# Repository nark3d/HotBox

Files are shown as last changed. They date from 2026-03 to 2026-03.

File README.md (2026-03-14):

# HotBox

HotBox - a tiny enclosure heater

## Contents

- [Disclaimer](#-disclaimer-)
- [BOM](#bom)
- [Note](#note)
- [Installation Instructions](#installation-instructions)
- [Klipper Config](#klipper-config)
- [Gotchas](#gotchas)
- [Inspiration and Credit](#inspiration-and-credit)

<p align="center">
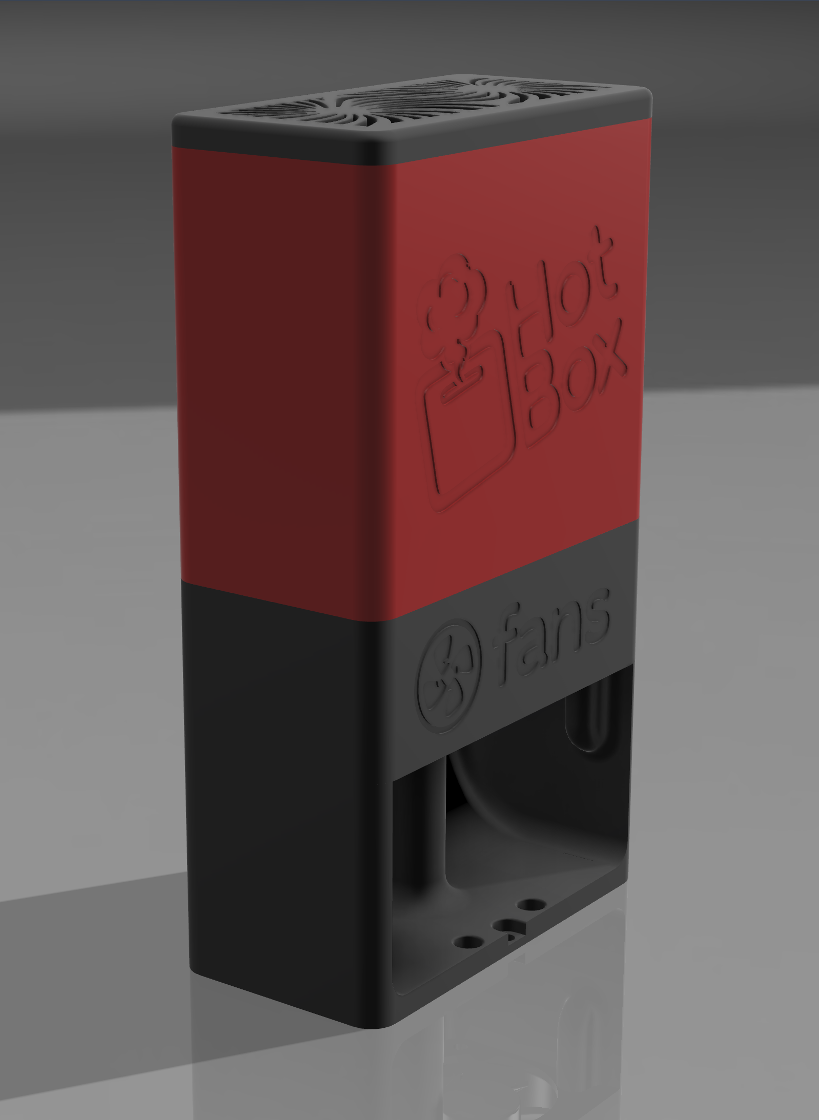
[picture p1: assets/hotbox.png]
HotBox

</p>

<p align="center"><em>100mm wide, 52mm deep and 177mm high</em></p>

<p align="center">
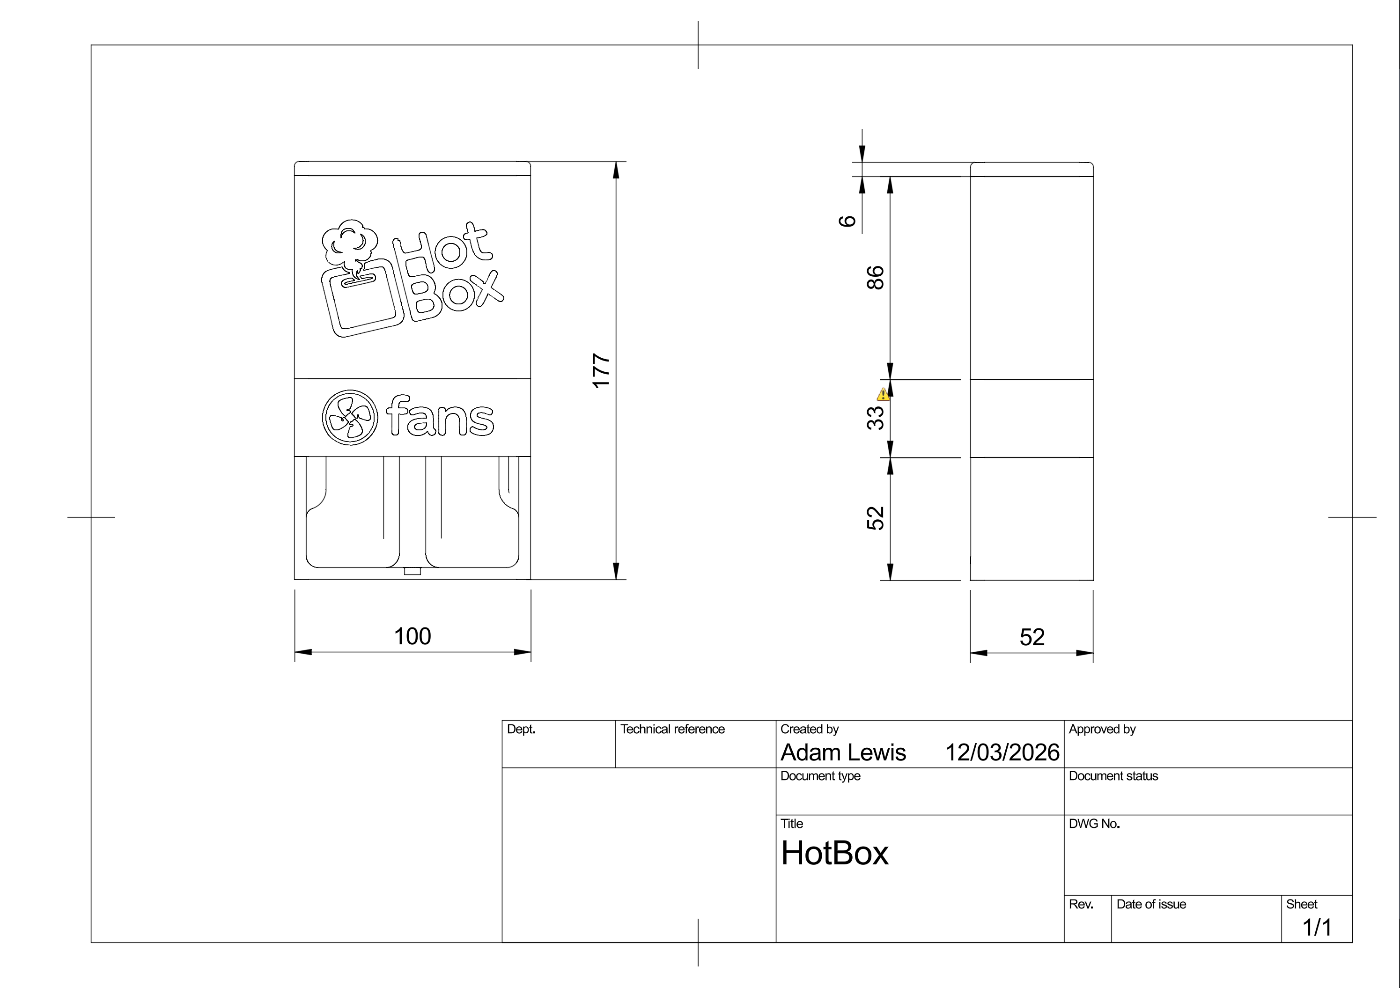
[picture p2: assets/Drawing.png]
HotBox Technical Drawing

</p>

# 🔥 Disclaimer 🔥

> [!WARNING]
> HotBox uses a resistive heating element inside an enclosed space. Built and configured incorrectly, it is a genuine fire risk.
>
> This project is shared as-is for experienced makers who understand the risks. The author accepts no responsibility for damage, injury, or loss of any kind. You build and run this entirely at your own risk.
>
> If you're not comfortable working with high-current DC systems and thermal management, please don't attempt this build.

# BOM

<p align="center">
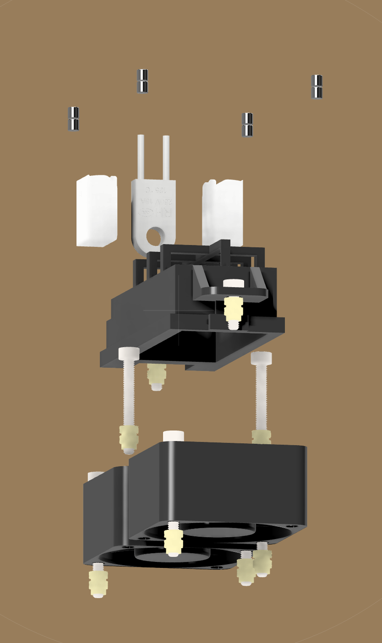
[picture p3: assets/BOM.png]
BOM

</p>

<p align="center">
<video src="https://github.com/user-attachments/assets/a794df79-9960-4280-891d-2e4521b5a101" width="50%" controls></video>
</p>

<table>
  <thead>
    <tr>
      <th>#</th>
      <th>Image</th>
      <th>Part</th>
      <th>Description</th>
      <th>Qty</th>
      <th>Notes</th>
      <th>Link</th>
    </tr>
  </thead>
  <tbody>
    <tr>
      <td>1</td>
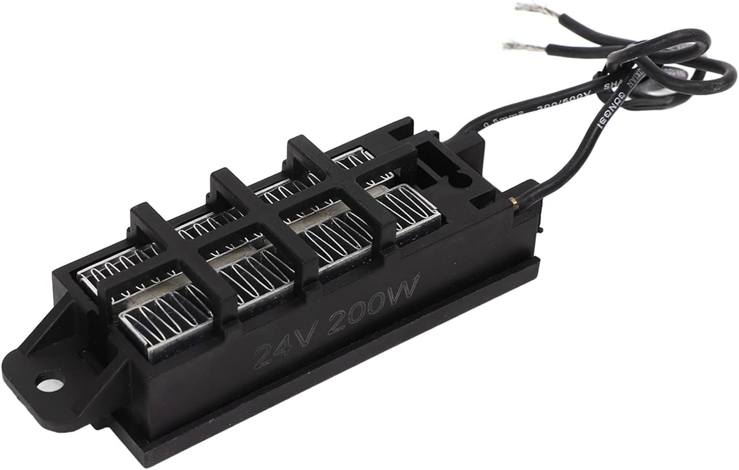
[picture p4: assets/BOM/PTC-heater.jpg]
PTC Heater
      <td></td>
      <td>PTC Heater Element</td>
      <td>24V 200W ceramic PTC heater</td>
      <td align="center">1</td>
      <td>Self-limiting; derate above 87°C</td>
      <td><a href="https://www.amazon.co.uk/dp/B0DK5W3RKS">amazon.co.uk</a></td>
    </tr>
    <tr>
      <td>2</td>
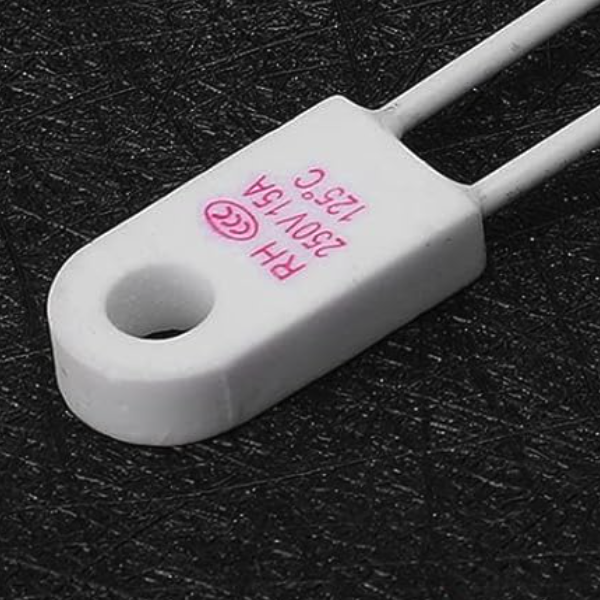
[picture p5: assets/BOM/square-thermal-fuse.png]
Thermal Fuse
      <td></td>
      <td>Square Thermal Fuse</td>
      <td>125°C Ceramic Thermal 250V 15A</td>
      <td align="center">1</td>
      <td>CQC rated; soldered inline</td>
      <td><a href="https://www.amazon.co.uk/dp/B0BNQ7SJYP">amazon.co.uk</a></td>
    </tr>
    <tr>
      <td>3</td>
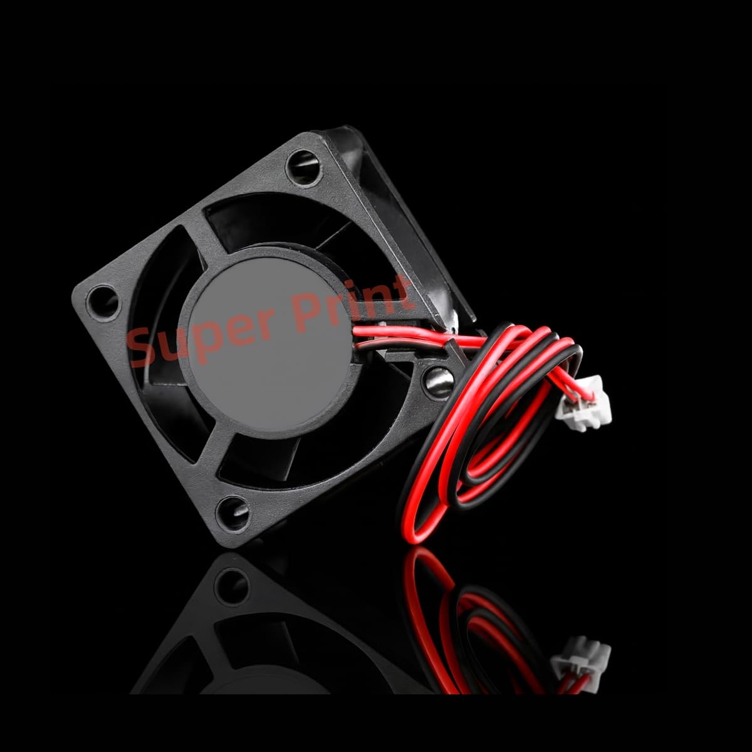
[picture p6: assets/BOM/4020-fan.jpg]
4020 Fan
      <td></td>
      <td>Axial Fan</td>
      <td>24V 4020 axial fan</td>
      <td align="center">2</td>
      <td>Must run at 100% when element is powered</td>
      <td><a href="https://www.amazon.co.uk/dp/B0FRFMXKSX">amazon.co.uk</a></td>
    </tr>
    <tr>
      <td>4</td>
      <td>
        <a href="assets/BOM/NTC-100K-thermistor-OD3mm.jpg">
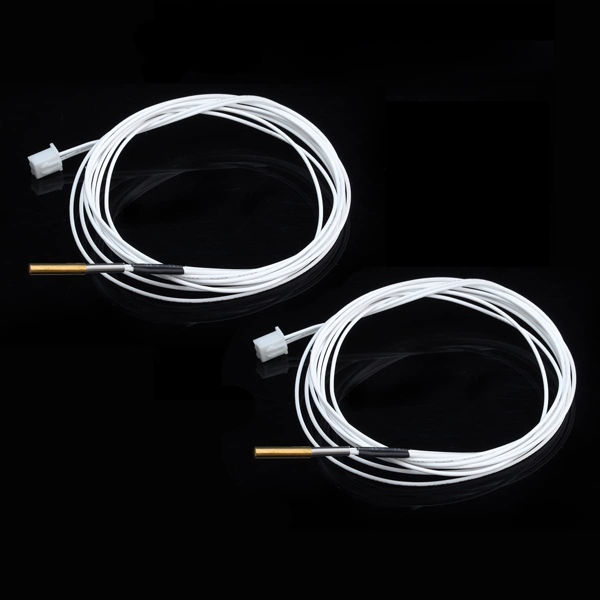
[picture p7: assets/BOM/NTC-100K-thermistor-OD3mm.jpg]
NTC 100K thermistor
            
        </a>
      </td>
      <td>Thermistor</td>
      <td>NTC 100K</td>
      <td align="center">1</td>
      <td>Seats in dedicated hole in PTC body; use thermal glue</td>
      <td><a href="https://www.amazon.co.uk/dp/B0BDFHZZQX?">amazon.co.uk</a></td>
    </tr>
    <tr>
      <td>5</td>
      <td>
        <a href="assets/BOM/thermal-glue.jpg">
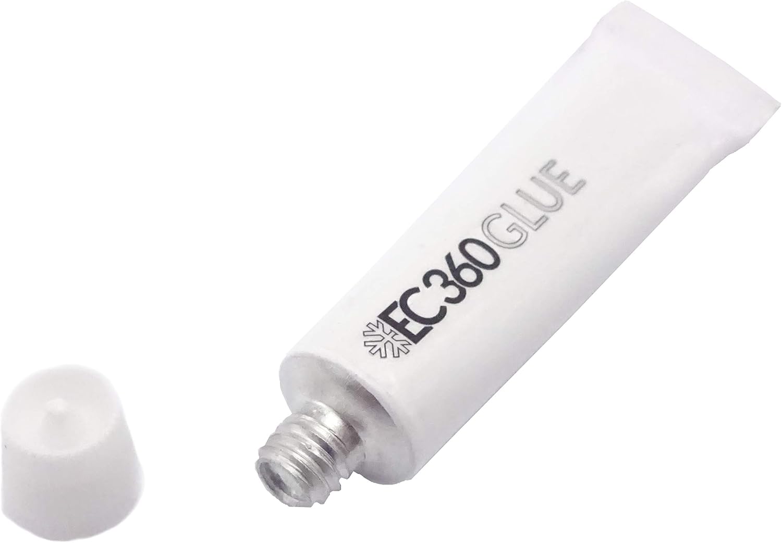
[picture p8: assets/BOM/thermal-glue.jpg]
Thermal glue
          
        </a>
      </td>
      <td>Thermal Glue</td>
      <td>EC360 2W/mK thermal adhesive</td>
      <td align="center">1</td>
      <td>Bonds thermistor to PTC element body</td>
      <td><a href="https://www.amazon.co.uk/dp/B00XQ9AZ8Y">amazon.co.uk</a></td>
    </tr>
    <tr>
      <td>6</td>
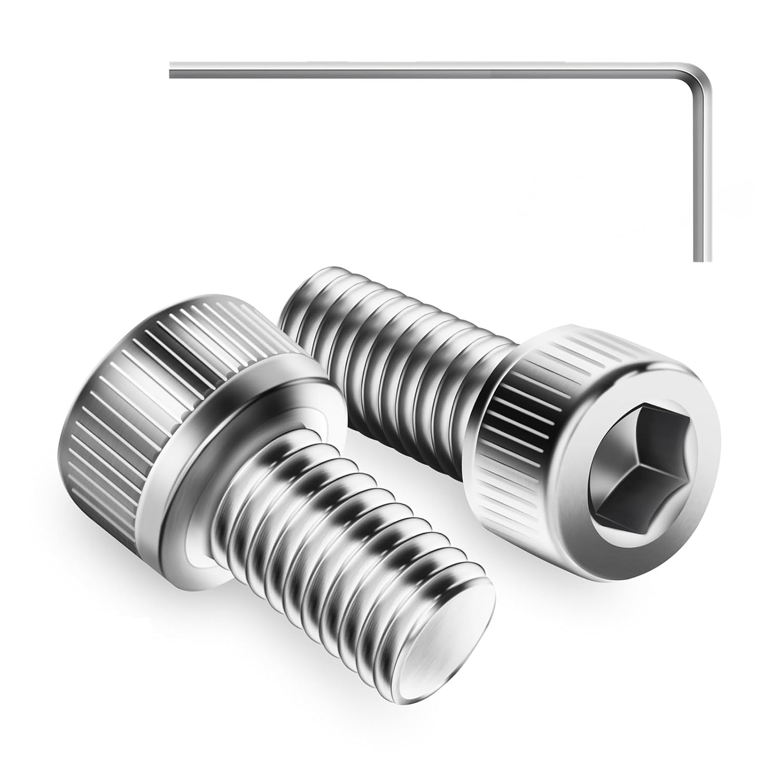
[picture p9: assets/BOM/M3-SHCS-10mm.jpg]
M3 SHCS
      <td></td>
      <td>M3×10mm SHCS</td>
      <td>Socket head cap screw</td>
      <td align="center">2</td>
      <td>Secures PTC heater element</td>
      <td></td>
    </tr>
    <tr>
      <td>7</td>
      <td><a href="assets/BOM/M3-SHCS-10mm.jpg">M3 SHCS</a></td>
      <td>M3×25mm SHCS</td>
      <td>Socket head cap screw</td>
      <td align="center">2</td>
      <td>Heater case to fan case</td>
      <td></td>
    </tr>
    <tr>
      <td>8</td>
      <td><a href="assets/BOM/M3-SHCS-10mm.jpg">M3 SHCS</a></td>
      <td>M3×30mm SHCS</td>
      <td>Socket head cap screw</td>
      <td align="center">4</td>
      <td>Fans through to fan duct</td>
      <td></td>
    </tr>
    <tr>
      <td>9</td>
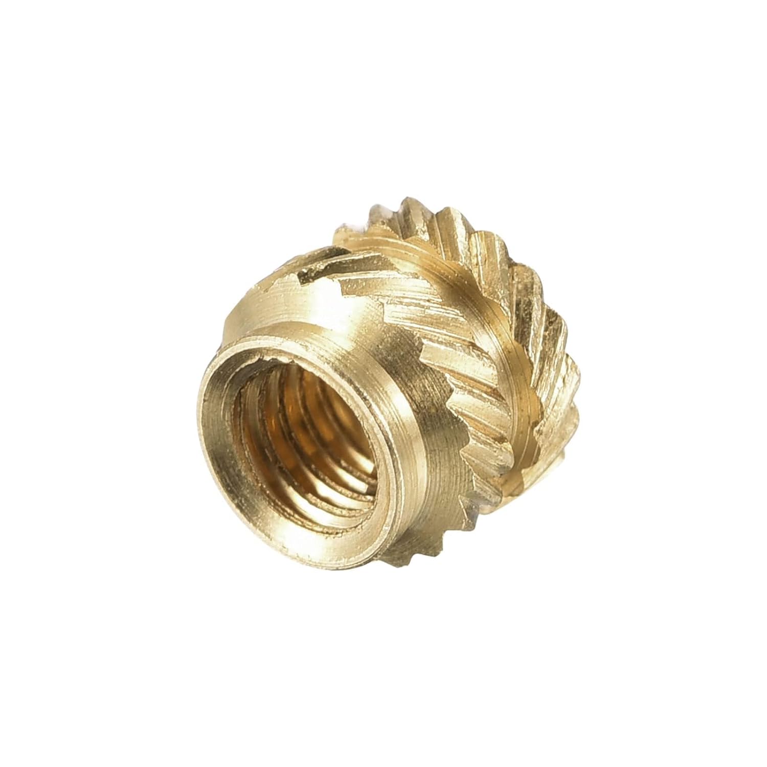
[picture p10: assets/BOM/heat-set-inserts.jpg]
Heat-Set Insert
      <td></td>
      <td>Heat-Set Insert</td>
      <td>M3×4mm brass heat-set insert</td>
      <td align="center">8</td>
      <td></td>
      <td><a href="https://www.amazon.co.uk/dp/B0DC6RXRB9">amazon.co.uk</a></td>
    </tr>
    <tr>
      <td>10</td>
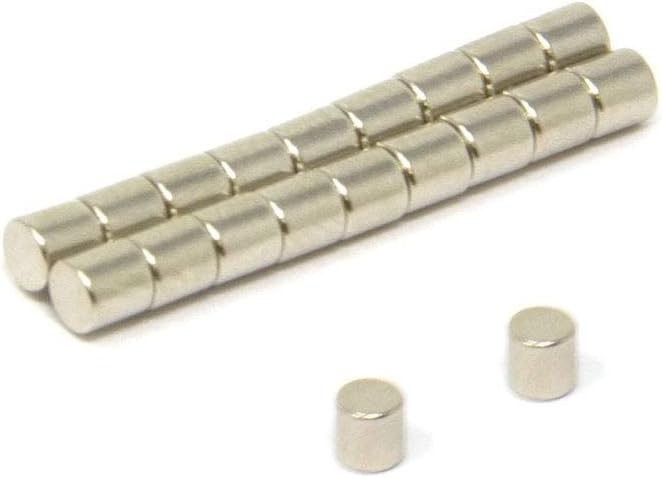
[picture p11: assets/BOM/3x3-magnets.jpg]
3x3mm Magnets
      <td></td>
      <td>Magnets</td>
      <td>3×3mm N42 neodymium magnets</td>
      <td align="center">8</td>
      <td>For lid retention</td>
      <td><a href="https://www.amazon.co.uk/dp/B00389GIK6">amazon.co.uk</a></td>
    </tr>
    <tr>
      <td>11</td>
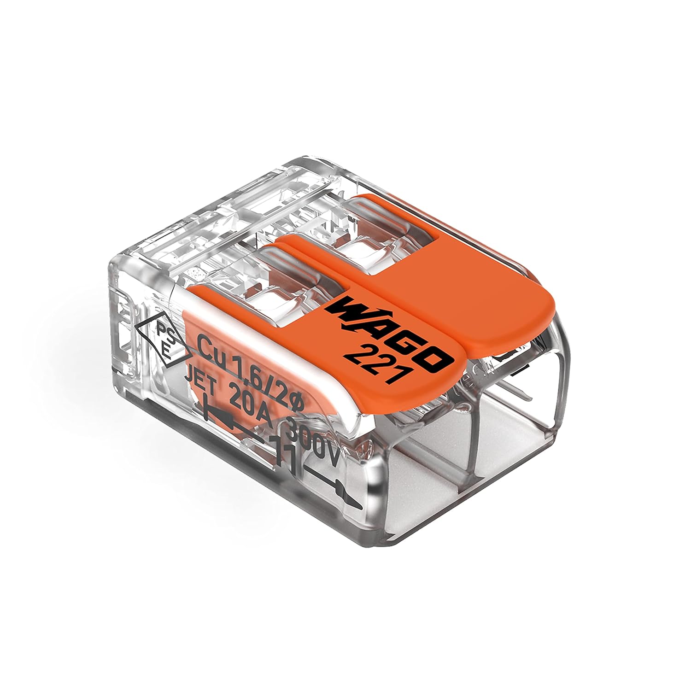
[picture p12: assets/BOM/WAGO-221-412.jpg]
WAGO 221-412
      <td></td>
      <td>WAGO 221-412</td>
      <td>2-conductor lever-nut splicing connector</td>
      <td align="center">3</td>
      <td>Tool-free wire connections for heater, fans and thermistor</td>
      <td><a href="https://www.amazon.co.uk/dp/B07W4RQ6R6">amazon.co.uk</a></td>
    </tr>
    <tr>
      <td>12</td>
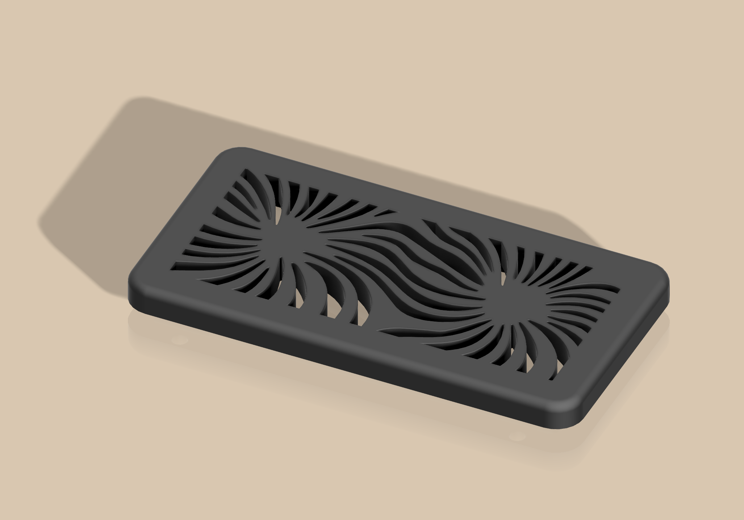
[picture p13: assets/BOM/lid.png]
Lid
      <td></td>
      <td>Lid</td>
      <td>Printed part</td>
      <td align="center">1</td>
      <td>Print in ABS/ASA</td>
      <td><a href="STLs/hotbox-lid-v1.0.stl">STL</a></td>
    </tr>
    <tr>
      <td>13</td>
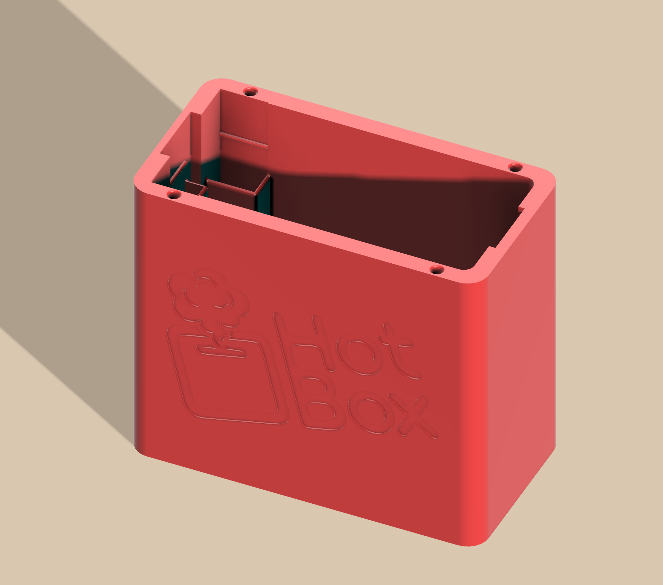
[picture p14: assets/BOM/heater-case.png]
Heater Case
      <td></td>
      <td>Heater Case</td>
      <td>Printed part</td>
      <td align="center">1</td>
      <td>Print in ABS/ASA</td>
      <td><a href="STLs/hotbox-heater-case-v9.3.stl">STL</a></td>
    </tr>
    <tr>
      <td>14</td>
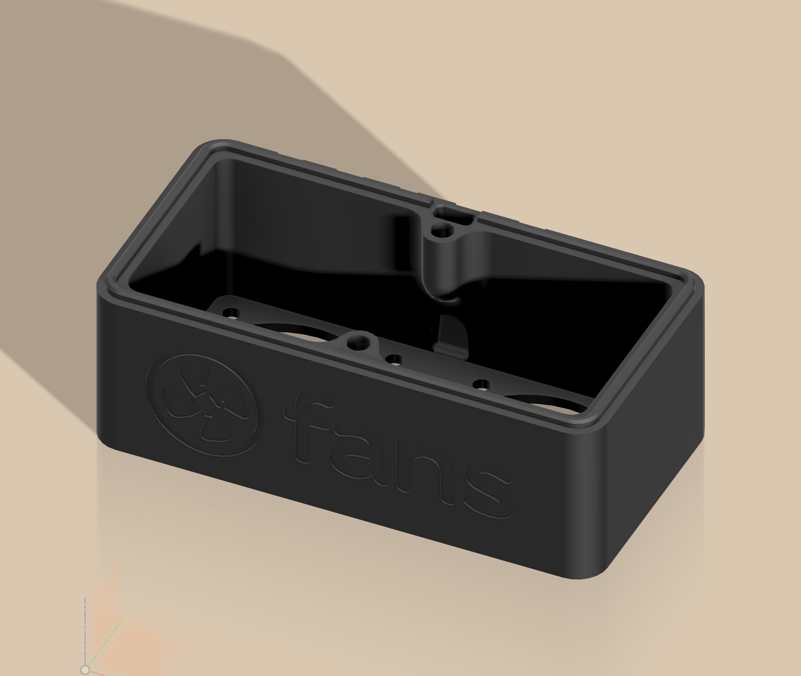
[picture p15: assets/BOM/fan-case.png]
Fan Case
      <td></td>
      <td>Fan Case</td>
      <td>Printed part</td>
      <td align="center">1</td>
      <td>Print in ABS/ASA</td>
      <td><a href="STLs/hotbox-fan-case-v4.2.stl">STL</a></td>
    </tr>
    <tr>
      <td>15</td>
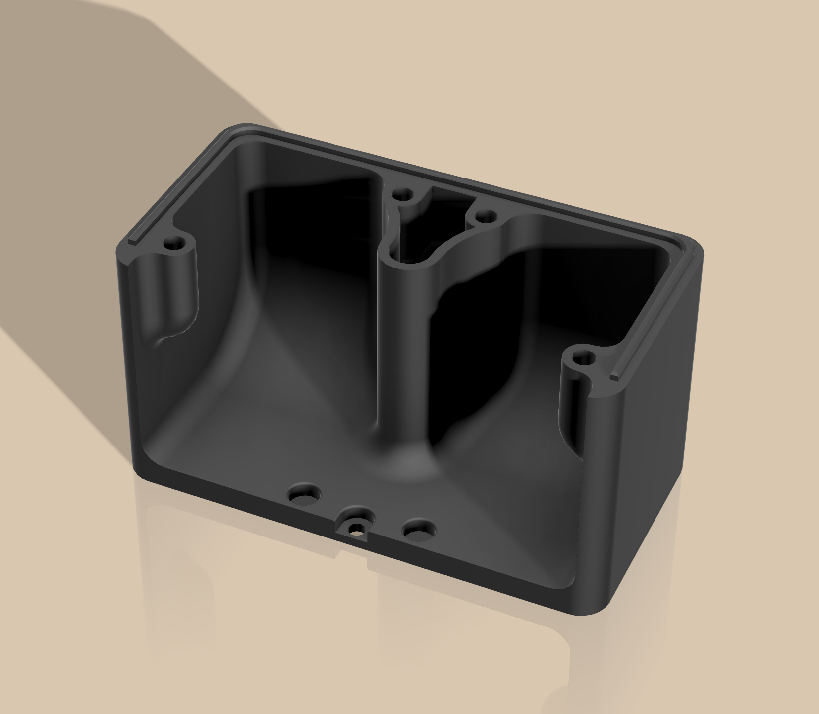
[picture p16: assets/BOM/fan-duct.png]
Fan Duct
      <td></td>
      <td>Fan Duct</td>
      <td>Printed part</td>
      <td align="center">1</td>
      <td>Print in ABS/ASA</td>
      <td><a href="STLs/hotbox-fan-duct-v2.1.stl">STL</a></td>
    </tr>
    <tr>
      <td>16</td>
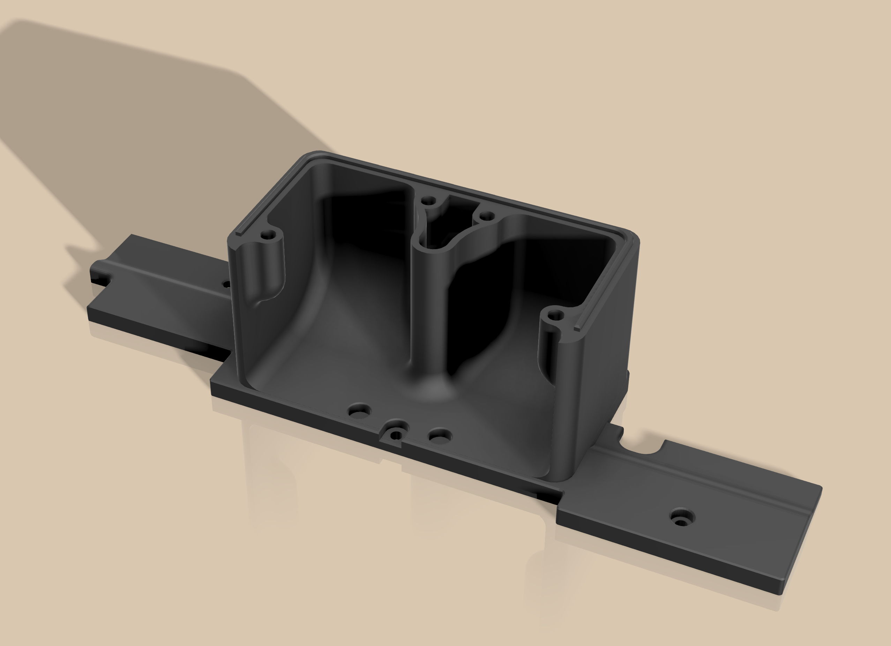
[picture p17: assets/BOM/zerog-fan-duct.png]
Fan Duct ZeroG Nebula
      <td></td>
      <td>Fan Duct ZeroG Nebula</td>
      <td>Printed part</td>
      <td align="center">1</td>
      <td>Print in ABS/ASA; alternative duct for ZeroG Nebula enclosure</td>
      <td><a href="STLs/hotbox-fan-duct-zerog-nebula-v2.1.stl">STL</a></td>
    </tr>
  </tbody>
</table>

# Note

<p align="center">
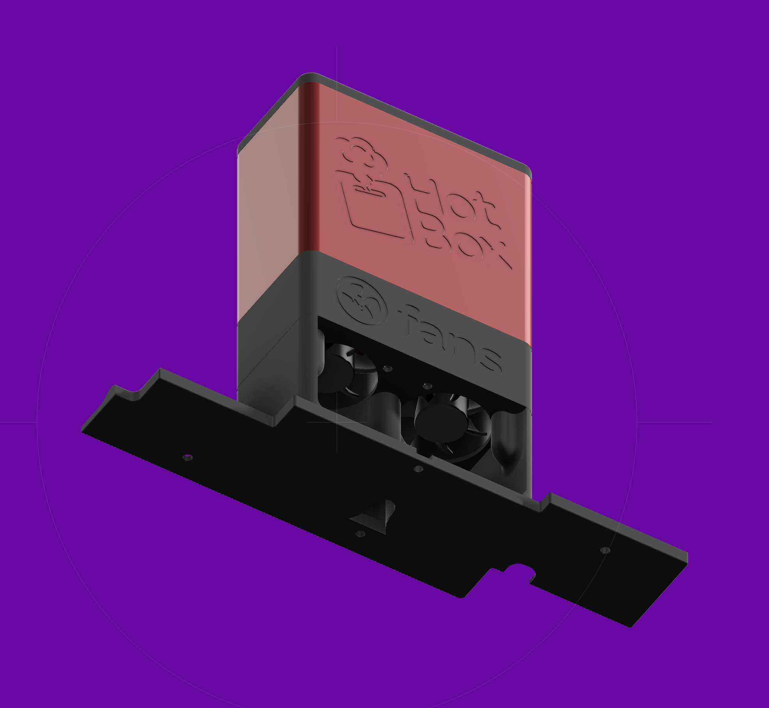
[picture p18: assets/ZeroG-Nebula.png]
ZeroG-Nebula

</p>

I made this for me on my ZeroG Nebula printer. I've provided a fan duct without the filler plate which will bolt onto a 2020 extrusion, but I'm not going to try and build mounting solutions for other printers without being able to test or measure.

If you want to use this heater on your printer, either:

- Modify the fan duct, test it, let me know and it can be added to the repo
- spec out what you need and I'll build it, (untested) and publish it

# Installation instructions

(Pictures to follow soon)

## Main body

- Fit all heat-set inserts into the correct holes with a soldering iron
- Trim the ends of the thermal fuse so that the wires fit neatly into the wagos without touching the lid
- Cut one side of the PTC thermal heater wire to length so that it fits in the wag opposite the cable hole without pushing the lid
- Fill the round hole in the PTC heater with thermal glue and insert the thermistor and wait to DRY (this will not cure until up to temperature later)
- Slot the WAGO's and thermal fuse into the correct holes
- Feed the wires through the cable hole. This will be SUPER TIGHT! The hole is as large as it can be whilst maintaining the small size of the heater
- Before pulling all the wires completely through, put the wired end of the PTC heater under the thermal fuse holder and then slot in the front. Wiggle it a bit and get it into position
- Screw down the PTC heater
- Pull the wires through so that they are neat and not obstructing the heater
- Push the wires through the fan case and down through the middle hole, but do not tighten
- Put the fans in the right position in the fan case - airflow going up into the PTC element
- Feed the fan wires through the middle hole
- Feed everything through the middle hole of the fan duct (you may need to join the PTC wire to a new piece of wire and shield it)
- Screw the fan case to the fan duct
- Keeping the wires tight with one hand push it all together
- Screw the heater case to the fan case
- Use a drop of superglue in the magnet holes and tap/push/force them in with something hard

## Electronics

<p align="center">
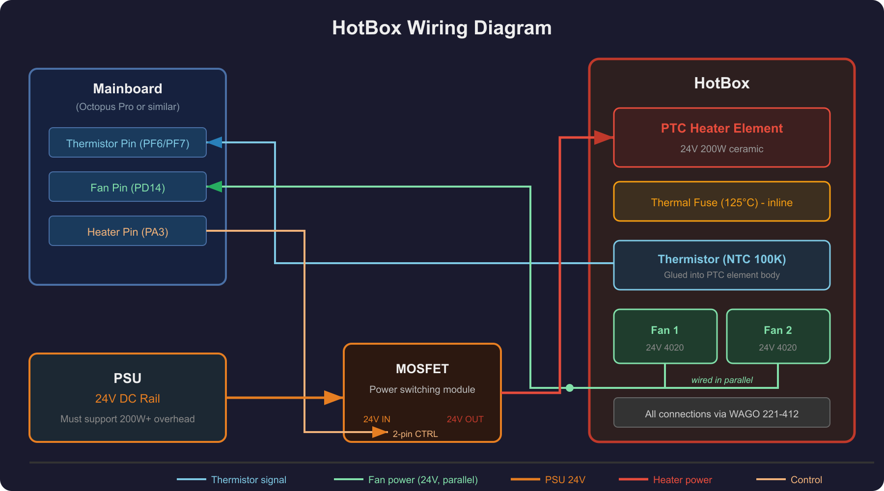
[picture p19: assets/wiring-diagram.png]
HotBox Wiring Diagram

</p>

This is very much dependent on your setup, but I did the following:

- Used WAGO's on the printer body to connect everything together to keep it neat
- Used a Mosfet running off the PSU and a fan PIN to modulate it
- Connected the thermistor and fans to the main board
- Configured everything in Klipper (see below)

# Klipper config

## printer.cfg

```ini
# ============================================================
# HOTBOX Config
# ============================================================

[heater_generic chamber]
heater_pin: PA3 # <---------------  change this
sensor_type: Generic 3950
sensor_pin: PF6 # <---------------  change this
min_temp: 0
max_temp: 70
control: pid
pwm_cycle_time: 0.01
pid_Kp: 100
pid_Ki: 0.3
pid_Kd: 30

[verify_heater chamber]
max_error: 600
check_gain_time: 300
hysteresis: 5
heating_gain: 0.5

# Fans will run at 100% any time the hotbox element exceeds 35, regardless
# of what Klipper is doing (PID calibration, printing, idle, anything).
[temperature_fan hotbox]
pin: PD14 # <---------------  change this
sensor_type: Generic 3950
sensor_pin: PF7 # <---------------  change this
min_temp: 0
max_temp: 120
target_temp: 35.0
min_speed: 0.0
max_speed: 1.0
control: watermark
max_delta: 1
kick_start_time: 0.5

# ============================================================
# HOTBOX CONTROL LOOP
# Runs every 5 seconds from printer startup
# Stores chamber target into HOTBOX_STATE so backoff can restart
# Fan speed is now managed automatically by [temperature_fan hotbox]
# This loop only handles: state tracking + overtemp backoff
# ============================================================
[delayed_gcode HOTBOX_CONTROL]
initial_duration: 5
gcode:
    {% set hotbox_temp = printer['temperature_fan hotbox'].temperature %}
    {% set chamber_target = printer['heater_generic chamber'].target %}
    {% set heater_on = chamber_target > 0 %}
    {% if heater_on %}
        SET_GCODE_VARIABLE MACRO=HOTBOX_STATE VARIABLE=target VALUE={chamber_target}
    {% endif %}
    {% if hotbox_temp > 87 and heater_on %}
        SET_HEATER_TEMPERATURE HEATER=chamber TARGET=0
        UPDATE_DELAYED_GCODE ID=HOTBOX_BACKOFF DURATION=60
        RESPOND MSG="HotBox: Element at {hotbox_temp}C - 60s backoff, will restart automatically"
    {% endif %}
    UPDATE_DELAYED_GCODE ID=HOTBOX_CONTROL DURATION=5

# ============================================================
# HOTBOX BACKOFF TIMER
# Triggered by HOTBOX_CONTROL after element overtemp
# Calls HOTBOX_RESTART after 60 seconds
# ============================================================
[delayed_gcode HOTBOX_BACKOFF]
initial_duration: 0
gcode:
    HOTBOX_RESTART

[include hotbox_macros.cfg] # <---------------  put this with your other includes or at the end of the file

```

## hotbox_macros.cfg

```ini
# ============================================================
# hotbox_macros.cfg
# HotBox enclosure heater user macros
# Include this file from printer.cfg with [include hotbox_macros.cfg]
# ============================================================

# ============================================================
# HOTBOX_STATE
# Stores the intended chamber target so backoff can restart
# This is set both by HOTBOX_ON and by the HOTBOX_CONTROL loop
# so it works whether you use the macro or set temp directly in Mainsail
# ============================================================
[gcode_macro HOTBOX_STATE]
variable_target: 0
gcode:

# ============================================================
# HOTBOX_ON
# Usage: HOTBOX_ON TARGET=60
# Heats enclosure to target temperature (default 60C, max 70C)
# Fans start automatically via [temperature_fan hotbox] - no manual control needed
# ============================================================
[gcode_macro HOTBOX_ON]
description: Heat enclosure to target temperature. Usage: HOTBOX_ON TARGET=60
gcode:
    {% set TARGET = params.TARGET|default(60)|float %}
    {% if TARGET > 70 %}
        RESPOND MSG="HotBox: Target {TARGET}C exceeds safe maximum of 70C - aborting"
    {% elif TARGET < 30 %}
        RESPOND MSG="HotBox: Target {TARGET}C is too low - minimum is 30C"
    {% else %}
        SET_GCODE_VARIABLE MACRO=HOTBOX_STATE VARIABLE=target VALUE={TARGET}
        SET_HEATER_TEMPERATURE HEATER=chamber TARGET={TARGET}
        UPDATE_DELAYED_GCODE ID=HOTBOX_CONTROL DURATION=5
        RESPOND MSG="HotBox: Heating enclosure to {TARGET}C - fans will run automatically"
    {% endif %}

# ============================================================
# HOTBOX_OFF
# Turns heater off and clears stored target
# Fans continue automatically until hotbox element cools below 40C
# ============================================================
[gcode_macro HOTBOX_OFF]
description: Turn off HotBox heater. Fans run automatically until hotbox cools below 40C
gcode:
    SET_GCODE_VARIABLE MACRO=HOTBOX_STATE VARIABLE=target VALUE=0
    SET_HEATER_TEMPERATURE HEATER=chamber TARGET=0
    RESPOND MSG="HotBox: Heater off - fans will run automatically until hotbox cools below 40C"

# ============================================================
# HOTBOX_STATUS
# Prints current hotbox status to console
# ============================================================
[gcode_macro HOTBOX_STATUS]
description: Report current HotBox temperatures and fan status
gcode:
    {% set hotbox_temp = printer['temperature_fan hotbox'].temperature %}
    {% set chamber_temp = printer['heater_generic chamber'].temperature %}
    {% set chamber_target = printer['heater_generic chamber'].target %}
    {% set fan_speed = printer['temperature_fan hotbox'].speed %}
    {% set intended_target = printer['gcode_macro HOTBOX_STATE'].target %}
    RESPOND MSG="HotBox Status:"
    RESPOND MSG="  Chamber temp: {chamber_temp}C / Target: {chamber_target}C"
    RESPOND MSG="  Hotbox element: {hotbox_temp}C"
    RESPOND MSG="  Fan speed: {(fan_speed * 100)|round}%"
    RESPOND MSG="  Stored target: {intended_target}C"

# ============================================================
# HOTBOX_RESTART
# Called automatically after 60s backoff - do not call manually
# Restarts heater using stored target if element has cooled below 75C
# ============================================================
[gcode_macro HOTBOX_RESTART]
description: Internal - restarts heater after backoff cooldown
gcode:
    {% set intended_target = printer['gcode_macro HOTBOX_STATE'].target %}
    {% set hotbox_temp = printer['temperature_fan hotbox'].temperature %}
    {% if intended_target > 0 %}
        {% if hotbox_temp < 70 %}
            SET_HEATER_TEMPERATURE HEATER=chamber TARGET={intended_target}
            RESPOND MSG="HotBox: Element cooled to {hotbox_temp}C - restarting heater to {intended_target}C"
        {% else %}
            RESPOND MSG="HotBox: Element still at {hotbox_temp}C - waiting another 60s"
            UPDATE_DELAYED_GCODE ID=HOTBOX_BACKOFF DURATION=60
        {% endif %}
    {% else %}
        RESPOND MSG="HotBox: No stored target - not restarting"
    {% endif %}
```

# Gotchas

- PID calibration may not work close to the enclosure's thermal limit. If the enclosure cannot reliably reach and re-reach the target temperature through multiple oscillation cycles, the calibration will fail. Try a lower target temperature (e.g. TARGET=50 instead of TARGET=60).

- PTC heater elements are self-limiting — they reduce power output as they approach their rated temperature. This makes PID calibration difficult as the element may throttle itself during the calibration oscillation cycles.

- Do NOT run PID_CALIBRATE with the fans configured as [fan_generic] controlled via delayed_gcode macros. Klipper holds the gcode queue during PID_CALIBRATE, which prevents delayed_gcode from executing, meaning fans will not run. This WILL cause the element to overheat. The fans MUST be configured as [temperature_fan] so they operate independently of the gcode queue.

- The hotbox fans must run at 100% whenever the PTC element is receiving power. This is not optional — the element will overheat and blow the thermal fuse without active cooling.

- Always let the fans cool the element down to 50 degrees or below before switching the machine off.

- There is a big thermal delay between the PTC element and the thermistor due to the distance between the two. Use thermal glue to bridge the gap, but factor this delay into any calculations.

- Running the PTC heater above 87°C for extended periods risks triggering the 125°C thermal fuse. The HOTBOX_CONTROL overtemp cutoff should be set to 87°C maximum.

- The thermistor must be seated directly in the dedicated hole in the PTC element body. Poor contact will cause it to read significantly below actual element temperature, meaning the emergency stop and overtemp cutoff will not trigger in time to protect the thermal fuse.

- The [temperature_fan] target is user-editable in Mainsail/Fluidd. Setting it above the element's safe operating temperature will prevent fans from running at the correct threshold. Do not modify this value.

- Klipper's max_temp on the [temperature_fan] section is an emergency shutdown threshold, not a cap on the settable target. Setting it too low will cause Klipper to hard-stop during normal operation.

- There needs to be enough overhead in the PSU to power a 200W PTC heater on the 24v rail, do the maths and ensure that there's enough power. If not, run an additional 200W DIN rail PSU or upgrade

- Do NOT use `control: watermark` for the chamber heater. Bang-bang switching of the heating element causes hard current transients on the shared 24V rail which affect TMC stepper driver behaviour, producing Z-axis banding artefacts on prints. Always use `control: pid` with `pwm_cycle_time: 0.01` to smooth current draw to a near-constant average.

# Shameless promotions

[Password Manager Reviews](https://passebo.com)

[VPN Reviews](https://thevpnadvisor.com)

[AI Image Generator Reviews](https://img-genius.com)

# Inspiration and credit

- [BentoBox](https://www.printables.com/model/272525-bentobox-v20-carbon-filter-for-bambu-lab-x1c-enclo) - I LOVE this and it was what triggered the idea for this design. Simple but effective in small spaces
- [BentoBox Fan Duct for ZeroG](https://www.printables.com/model/1496065-bentobox-fan-duct-for-zerog-nebula-255) - This is an absolutely great idea and I used the theory to build a similar integration for HotBox

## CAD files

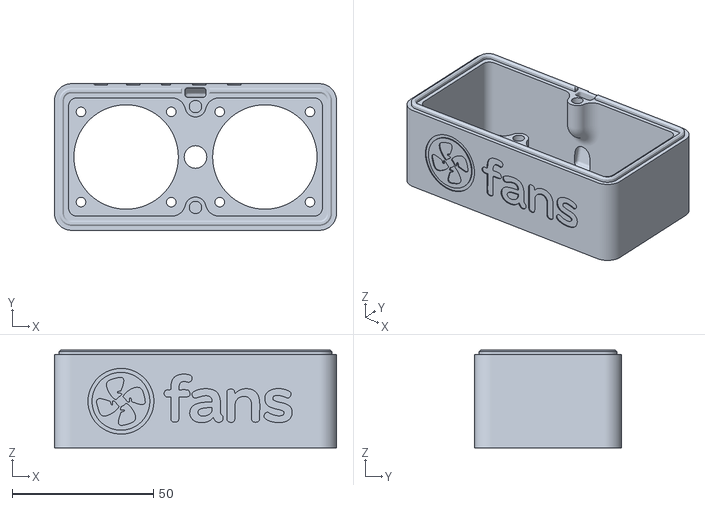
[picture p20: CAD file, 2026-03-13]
STLs/hotbox-fan-case-v4.2.stl
100.0 x 52.0 x 34.6

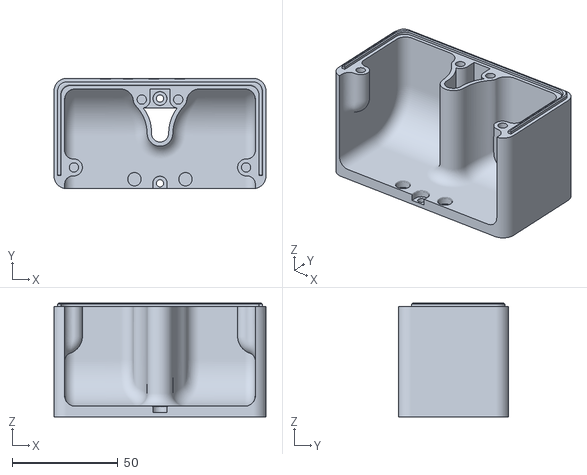
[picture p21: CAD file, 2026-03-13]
STLs/hotbox-fan-duct-v2.1.stl
100.0 x 52.0 x 53.6

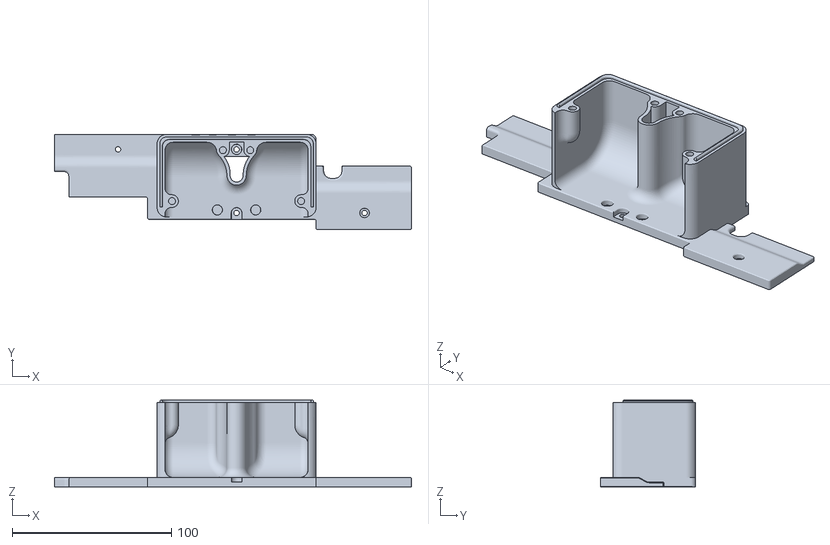
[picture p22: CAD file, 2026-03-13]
STLs/hotbox-fan-duct-zerog-nebula-v2.1.stl
224.5 x 60.0 x 54.6

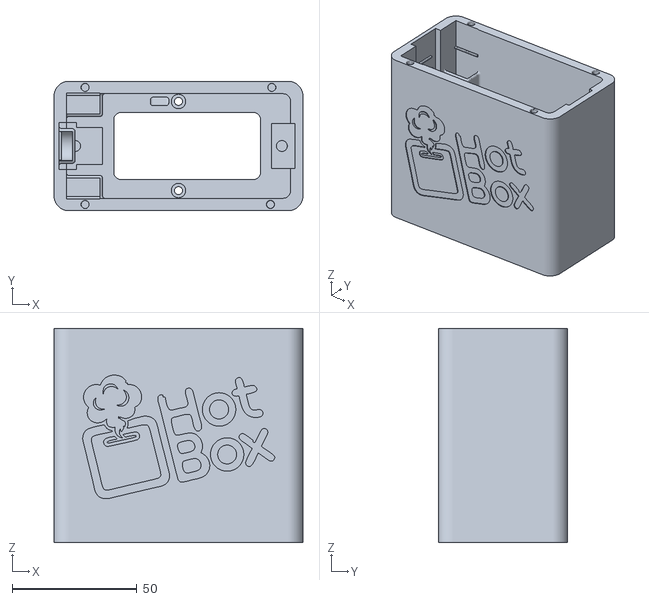
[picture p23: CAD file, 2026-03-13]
STLs/hotbox-heater-case-v9.3.stl
100.0 x 52.0 x 86.0

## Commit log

2026-03-13 Adding more docs and STLs
    [hotbox-fan-case-v4.2.stl, hotbox-fan-duct-v2.1.stl, hotbox-fan-duct-zerog-nebula-v2.1.stl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]
2026-03-13 Adding in wiring diagram
2026-03-14 Add wiring diagram and assembly video
    Made-with: Cursor
2026-03-14 Fixing BOM list
